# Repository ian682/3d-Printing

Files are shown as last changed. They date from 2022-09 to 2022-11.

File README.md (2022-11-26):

# X5SA Pro EVA 3.0 toolhead mod.

<p align="center">
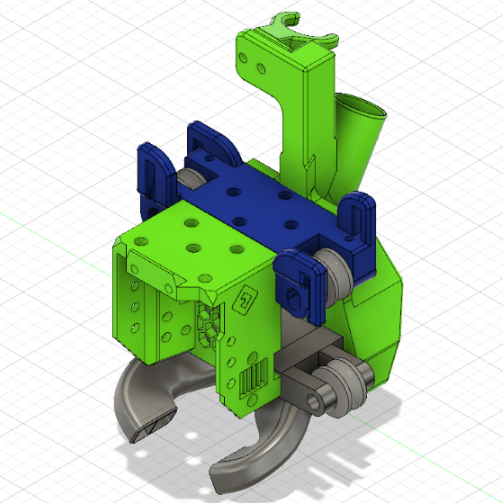
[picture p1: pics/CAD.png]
CAD Layout
  
</p>

Mod is based on the Heat Insert EVA 3.0 project located at https://main.eva-3d.page/

The insert size EVA is modeled for is M3 x D4.6 x L4.0 but this does not have to be exact, i.e. D5.0 or L5.0 inserts should work as well, just might require a bit of clean up of the plastic that's pushed out.

**26-Nov-2022 Update:** Increased OSG Linear bearing adjustment range on "tronxy eva top."  
**24-Nov-2022 Update:** Updated Standard and Volcano duct STLs to stiffen bearing attachment and allow a higher bearing tension range. Also updated step and STL files for the top to adjust geometry for duct changes. Uploaded Step files for standard and volcano ducts, and uploaded fusion 360 ([Project Files](https://github.com/ian682/3d-Printing/blob/main/cad/EVA3/x5sa-pro_eva3_cad.f3d)) for easier CAD maintenance.  
**15-Nov-2022 Update:** Added cable holder for cable bundles.  
**8-Nov-2022 Update:**  Added an additional version of the CPAP back with tilted inlet.   
**30-Oct-2022 Update:** Made CPAP/remote cooling back for 18mm hose.  
**21-Oct-2022 Update:** Increased belt adjustment range on (tronxy eva top.stl) and (tronxy eva top.step) files.

# X5SA Pro EVA 3.0 Mod BOM:

9x Heat inserts  
4x m5 x 30mm screws for OSG Rail Bearings  
14x M5 washers for OSG Rail Bearings  
4x m5 nuts for OSG Rail Bearings  
4x m3 x 40mm screws for mounting universal front to the back 35mm will also work, I only had 40mm on hand. 
2x m3 x 18mm screws for mounting 5015 fans  
4x m3 x 12mm screws osg bearing to rail pre tension  
1x m3 x 10mm screw to mount back to fan duct
2x m3 x 10mm screws to mount cable chain  
2x m3 nuts to mount cable chain  
2x M3 x 30mm screws to mount cable chain bracket to the spacer.  
2x m3 x 6mm screws to mount X-endstop  
1x back ([Dual 5015](https://github.com/ian682/3d-Printing/blob/e409669026c80c21ba648143a89b0567bc5072f4/EVA3/dual%205015%20back.stl) or [Remote Air/CPAP](https://github.com/ian682/3d-Printing/blob/ee2263dbc57e0aab3029547079da61b6ebe15152/EVA3/CPAP%20Back%20Type%202.stl))  
1x X5SA pro EVA Top ([EVA3/tronxy eva top.stl](https://github.com/ian682/3d-Printing/blob/1bf0406b388527418f87d238a55095cb1d77b1a6/EVA3/tronxy%20eva%20top.stl))  
1x X5SA pro EVA fan duct. Choice depends on hotend length. ([Standard Duct](EVA3/EVA_3-0_X5SA-PRO_Standard_Duct.stl) or [Volcano Duct](EVA3/EVA_3-0_X5SA-PRO_Volcano_Duct.stl))  
2x Duct plugs ([EVA3/Duct Hole Plug.stl](https://github.com/ian682/3d-Printing/blob/1bf0406b388527418f87d238a55095cb1d77b1a6/EVA3/Duct%20Hole%20Plug.stl))  
1x Cable chain spacer ([EVA3/cablechain spacer.stl](https://github.com/ian682/3d-Printing/blob/1bf0406b388527418f87d238a55095cb1d77b1a6/EVA3/cablechain%20spacer.stl))  
1x Optional [Cable Holder](https://github.com/ian682/3d-Printing/blob/483a43ff8f26261a6c29b435dc45ae465c516c85/EVA3/Cable%20holder.stl) 

# Main Eva Parts BOM: 
STLs are grabbable from https://main.eva-3d.page/heat_insert/core/corexy/#bill-of-materials  
EVA moddels will list needed screws and heat insert quantaty along with any other needed items. If you do not see a mount for your hotend or extruder, check on printables and thingiverse. Baring that, a lot of models get posted to the EVA section of the Rat Rig Comunity discord https://discord.gg/FekS7xaR New mounts for extruders and hotends are created most days.

Universal front
Hotend mount of your choice  
extruder/drive mount of your choice  
Probe mount of your choice  
shroud if desiered; extra weight and not needed  

# Other Suggested Mods:
Proper belt tension system, suggested version https://www.thingiverse.com/thing:4605033

# Instructions
1st get all needed washers, screws, nuts, ptfe tubing, etc that you need.  
2nd Print desired STL files.  

Print orientation for X5SA pro Parts:  
<p align="center">
  Print orientation
</p>  

Supports will be needed for the X5SA pro EVA top and the bearing arms on the duct. the duct section of the back may or may not need supports depending on how well your printer can bridge.  

After everything is printed, I suggest installing the heat inserts and dry fitting the printed parts together to make sure they all fit and you have everything you need.

Heat insert locations on mod parts:  
<p align="center">
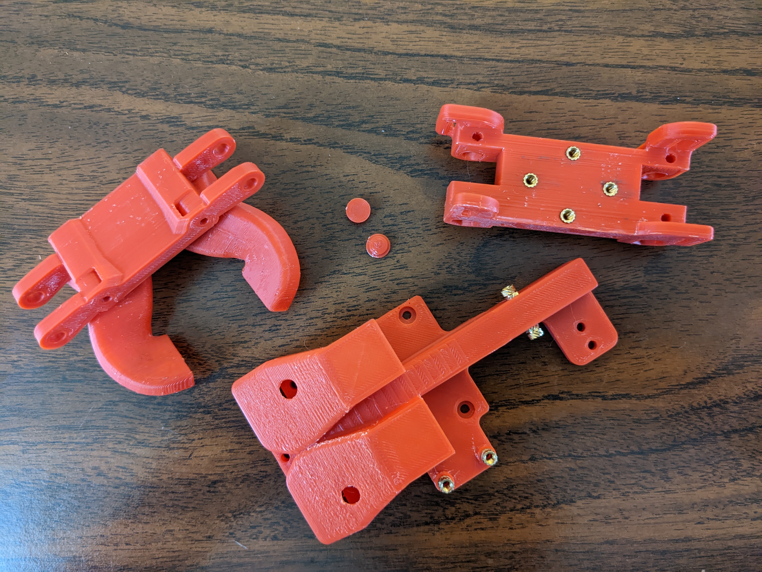
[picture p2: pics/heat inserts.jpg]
Back inserts
  
</p>  

Don't forget the one in the duct:  
<p align="center">
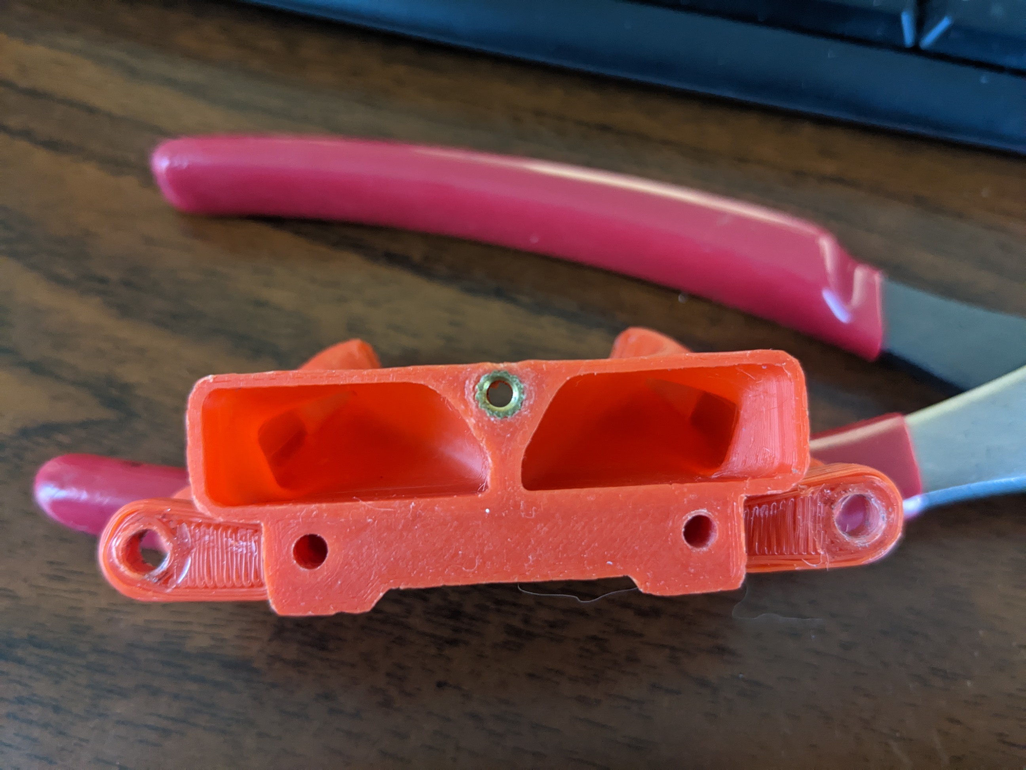
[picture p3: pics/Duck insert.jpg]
Duct insert
  
</p> 
After installing all the heat inserts in the mod parts and the original EVA parts, assuming you have done a drie fit, you are ready to take apart the old tool head and install the new one. You will need the OSG bearing wheels from the old printhead plate, thats the wheels that ride on the rail. I chose to install connectors for the fans, hotend, and ABL sensor. It makes changes and installs much easier.  

Start with installing the OSG bearings in the top and duct bottom. The doct bottom is the easiest of the two to do, so you may want to start with that. Each bearing will get one or two washers, depending on thickness, that go against it on the side that that indents. One side of the bearing protrudes and the other is indented. the washer needs to fit a little loose inside that part of the bearing or it may cause friction. I chose to face the protruding side of the bearings facing the front. It doesn't matter if it faces the front or back, but all 4 must face the same direction.

Top with bearing parts:
<p align="center">
  Top part
</p>   

In this case, all 4 of the bearing required two washers to fill up the space for the bearings. Remember, the washers go on the side that doesn't protrude. For the m5 x 30mm screws, you will need to put a washer on the screw before you start installing it or it will stick out just a little to far. So the order is, washer onto m5 screw > insert screw into top or bottom > insert bearing and start putting the screw through it > two washers > out the other side of the bearing holder arms > nut. The bottom duct will also get another washer just before the nut, but the top does not get that washer. You can tighten the screws on the bottom duct bearings, but leave the ones for the top bearings loose so they can tension on the rail later.

<p align="center">
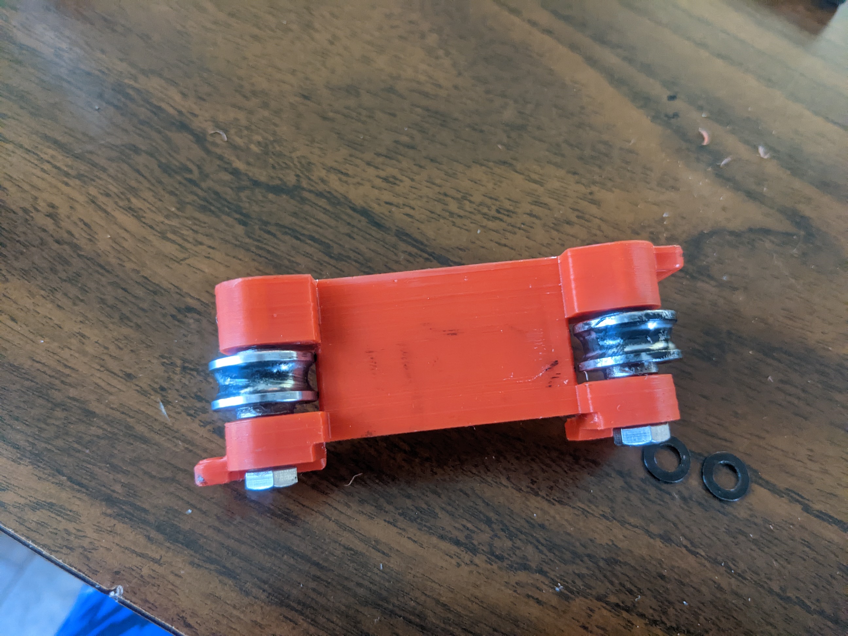
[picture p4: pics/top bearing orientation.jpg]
Top OSG orientation
  
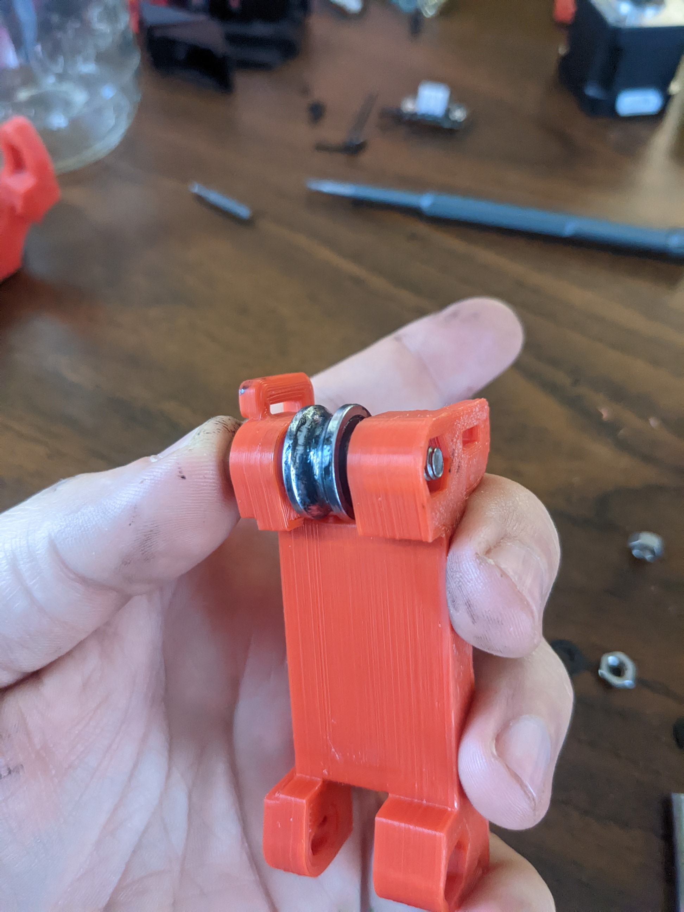
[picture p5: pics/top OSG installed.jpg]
Top OSG
  
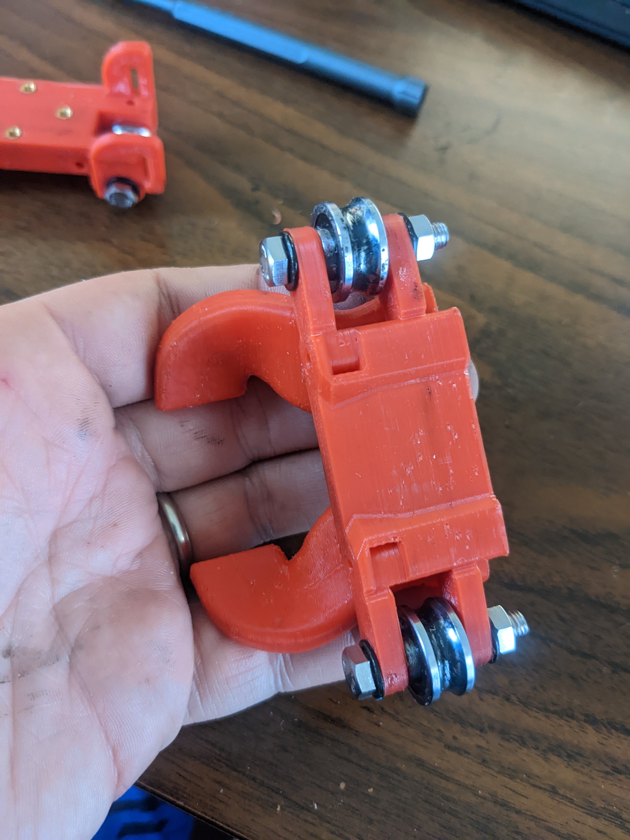
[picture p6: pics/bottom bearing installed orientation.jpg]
Bottom bearing installed
  
</p> 

After this is done, you can build out the Universal front for the print head.

<p align="center">
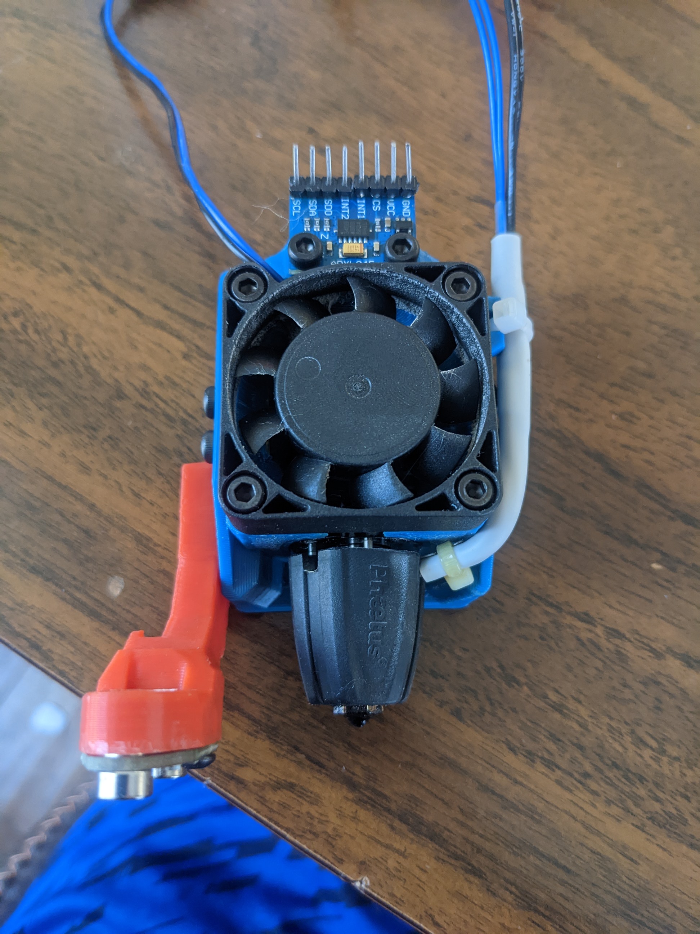
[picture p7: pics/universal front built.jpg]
Universal Front Completed
  
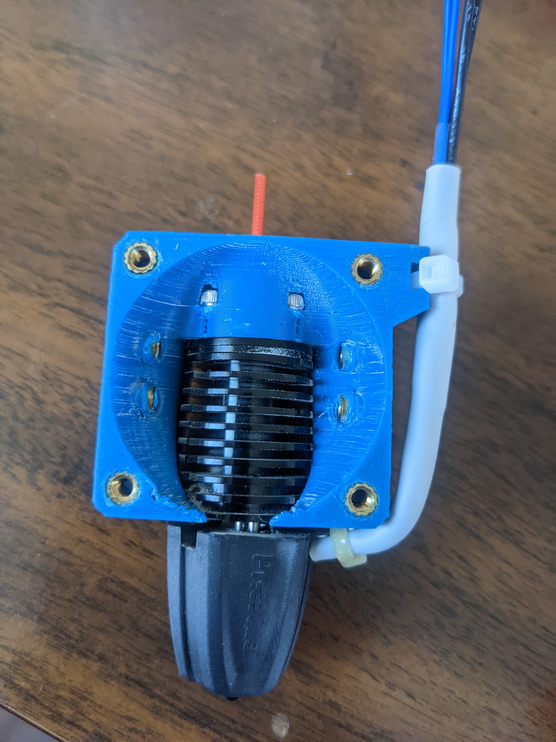
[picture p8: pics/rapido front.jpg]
Hotend Mount front
  
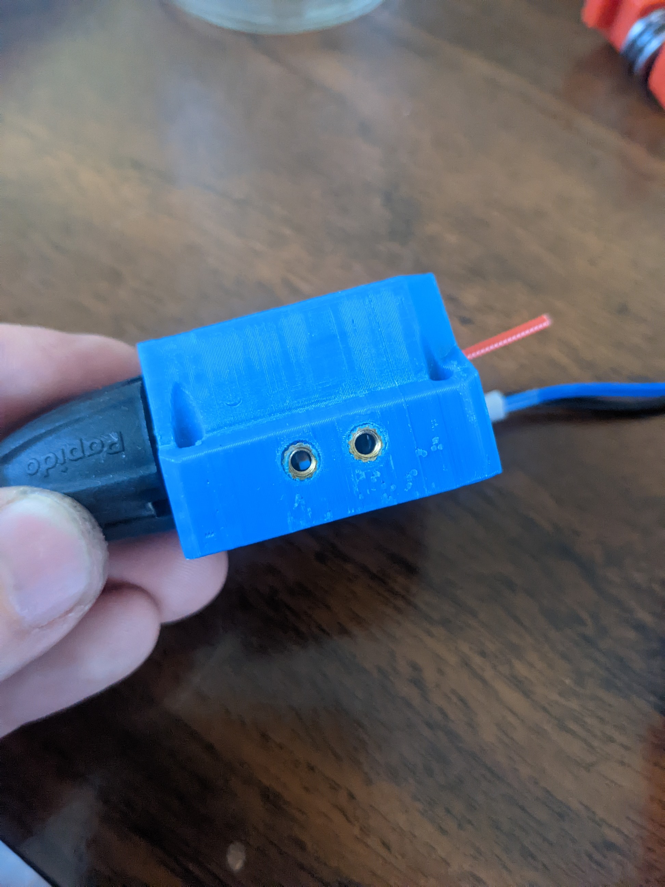
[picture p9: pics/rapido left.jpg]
Hotend Mount left
  
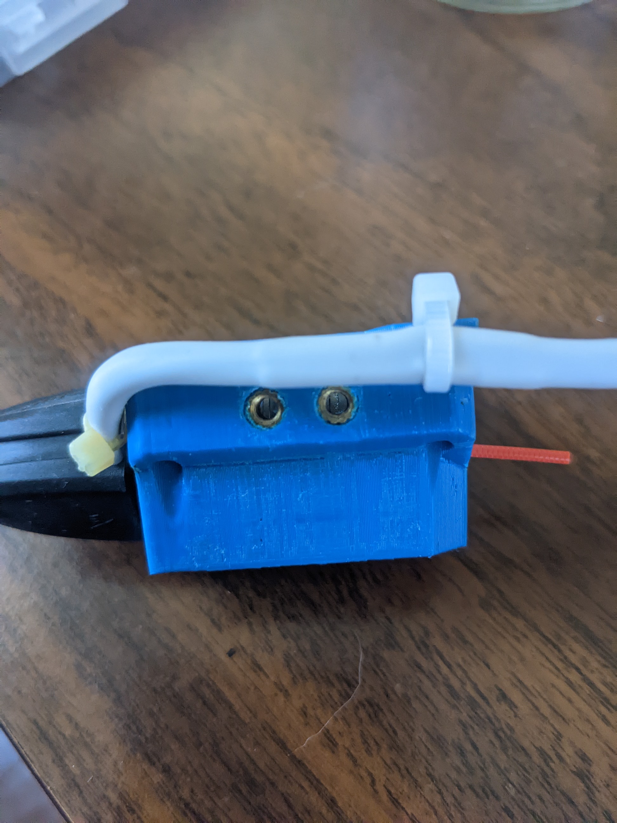
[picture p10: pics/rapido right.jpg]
Hotend mount right
  
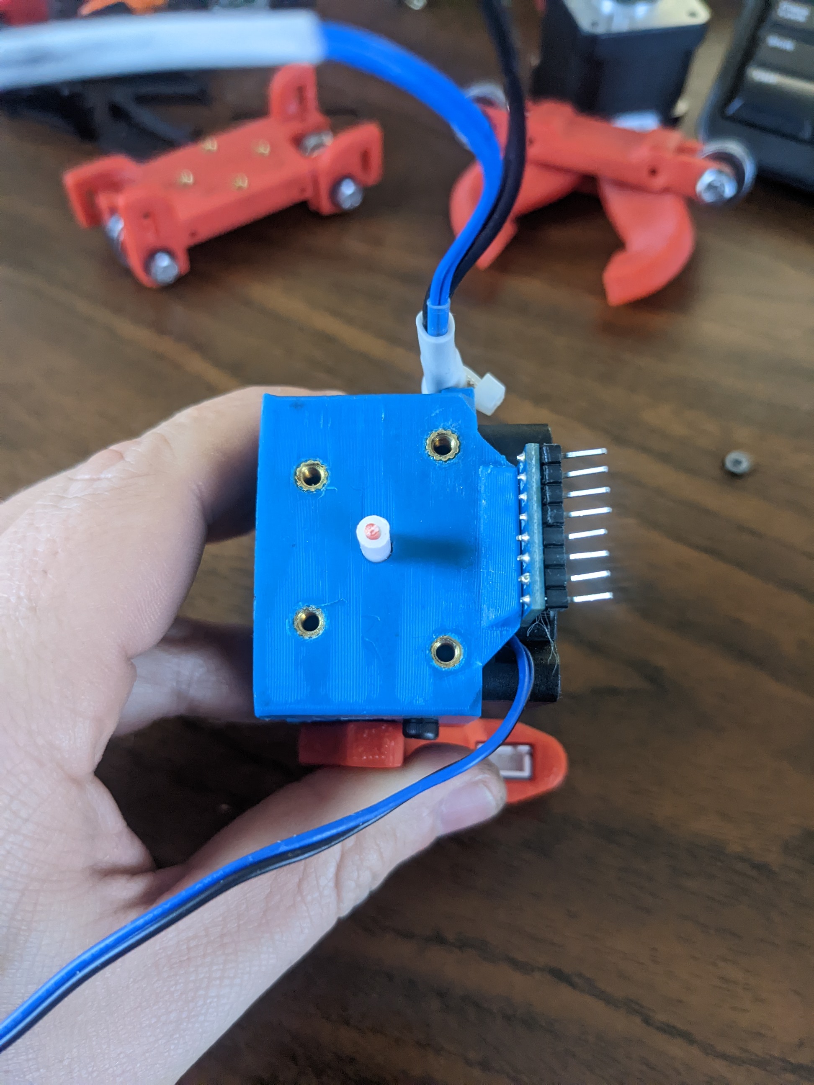
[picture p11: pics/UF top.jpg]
Universal Front top
  
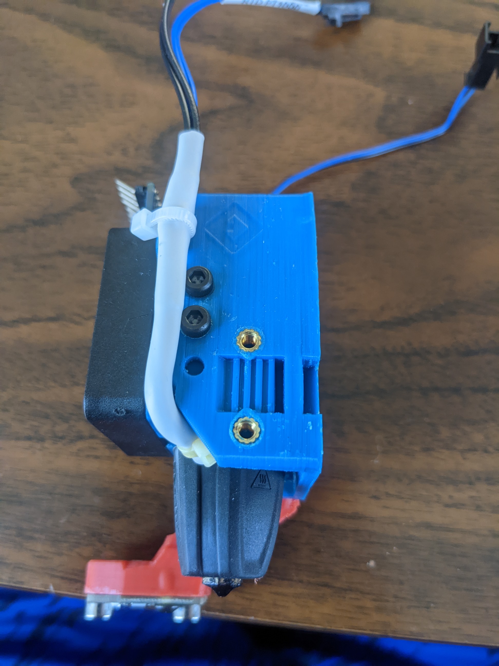
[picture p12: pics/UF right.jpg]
Universal Front right
  
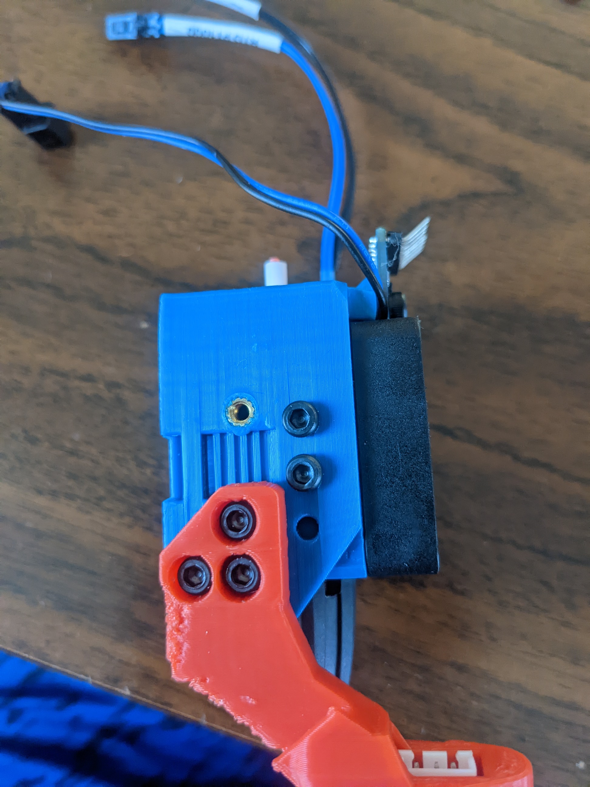
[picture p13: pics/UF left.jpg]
Universal Front left
  
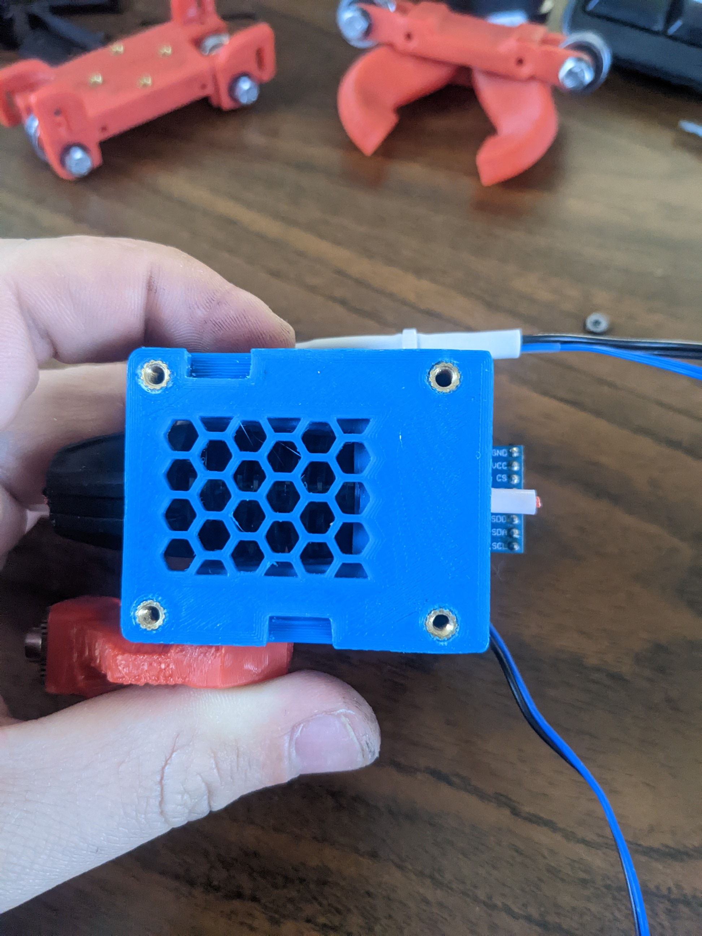
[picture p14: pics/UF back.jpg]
Universal Front back
  
</p>  

At this point you are ready to start installing. There are two changes need so that you don't run into anything at the back of the printer. 1st, install the spacer to push the cable chain holder further back. This gets 2 heat inserts at the back of it and uses two 20mm m3 screws and washers to attach the metal plate to it. You then re-use the m4 screws and t-nuts to insall the spacer on the rail again. 2nd, the stock X5SA cable breakout box need moved so it attaches to the bottom of the back rail instead of the top.
<p align="center">
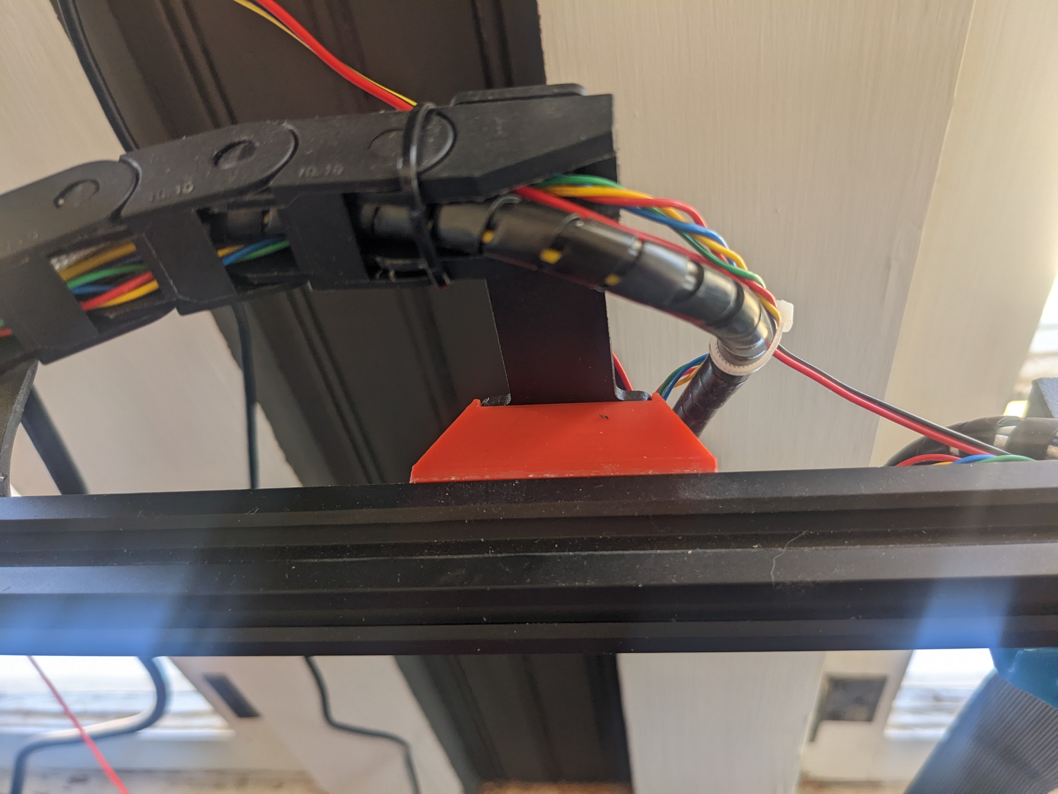
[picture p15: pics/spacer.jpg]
Cable chain spacer
  
  Breakout box moved
</p>  

Next you can mount the cable chain to the back plate of the EVA mod. Two m3 x 10mm screw are used for this along with washers and nuts.
<p align="center">
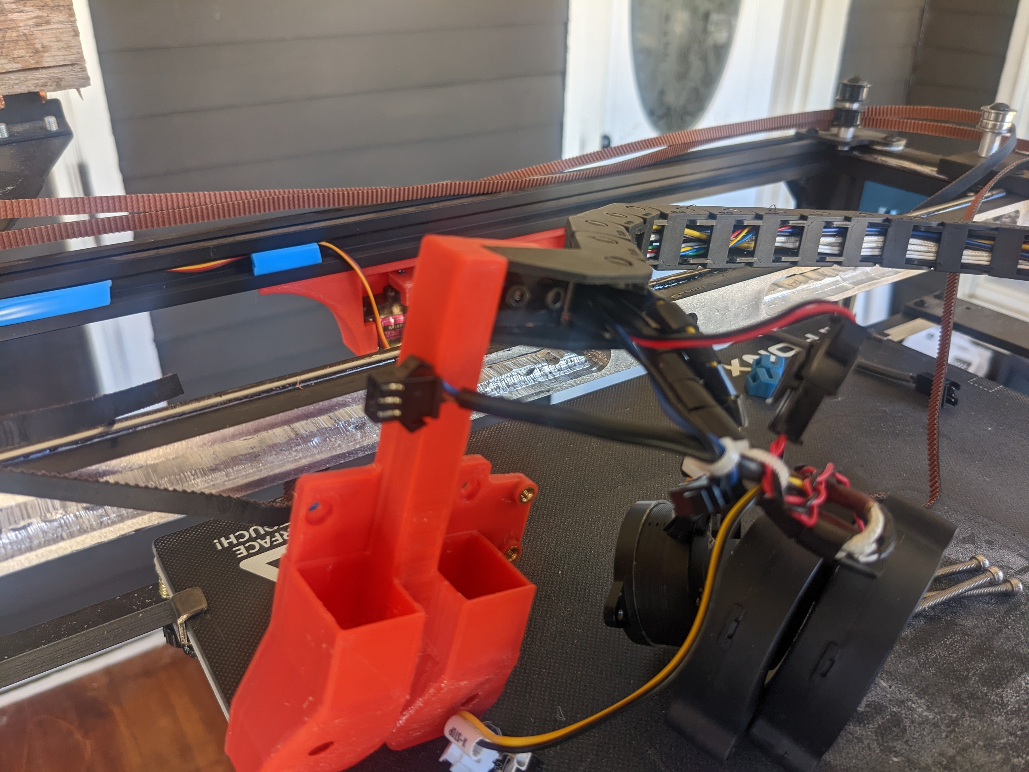
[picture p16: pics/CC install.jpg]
Cable chain installed
  
</p> 

Now install the 4x m3 x 40mm scews through the back plate.
<p align="center">
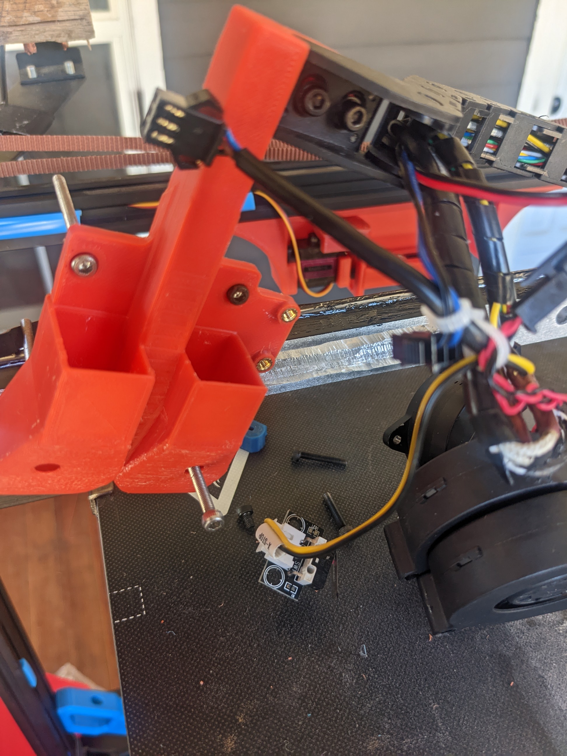
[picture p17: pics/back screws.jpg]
Back screws
  
</p> 

And slide on the bottom duct. Don't miss installing the m3 x 10mm screw from the back into the duct.
<p align="center">
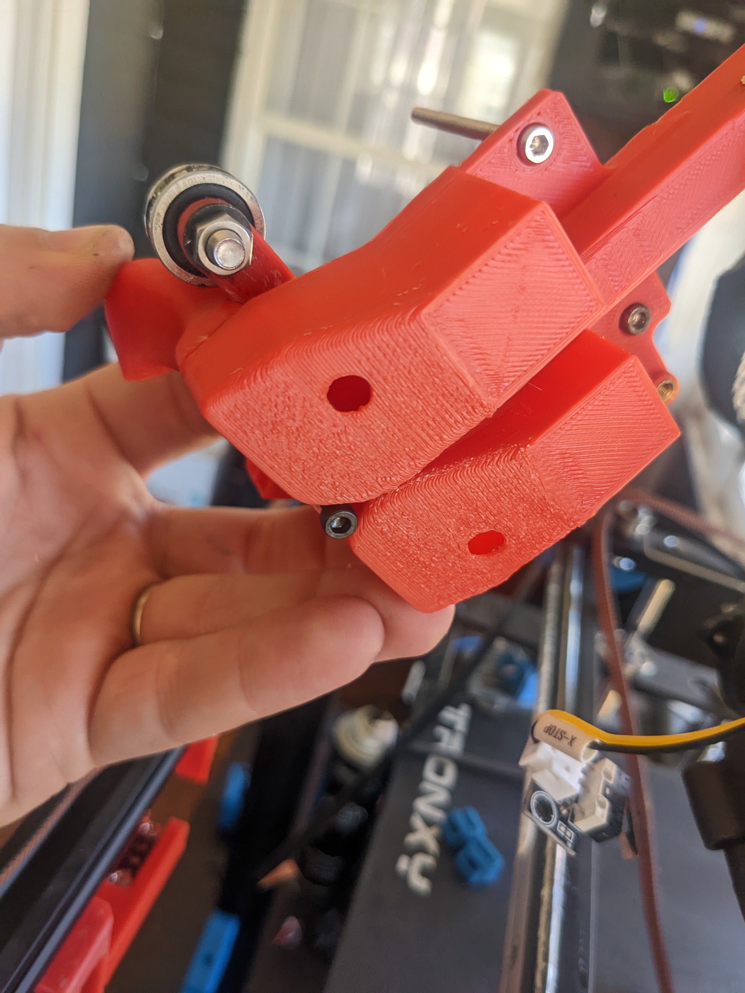
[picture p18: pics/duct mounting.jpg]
Mounting duct
  
</p> 

Move the printhead so that the OSG rail bearings on the duct mate to the bottom of the rail and install the X5SA EVA top onto the m3 x 40mm screws.
<p align="center">
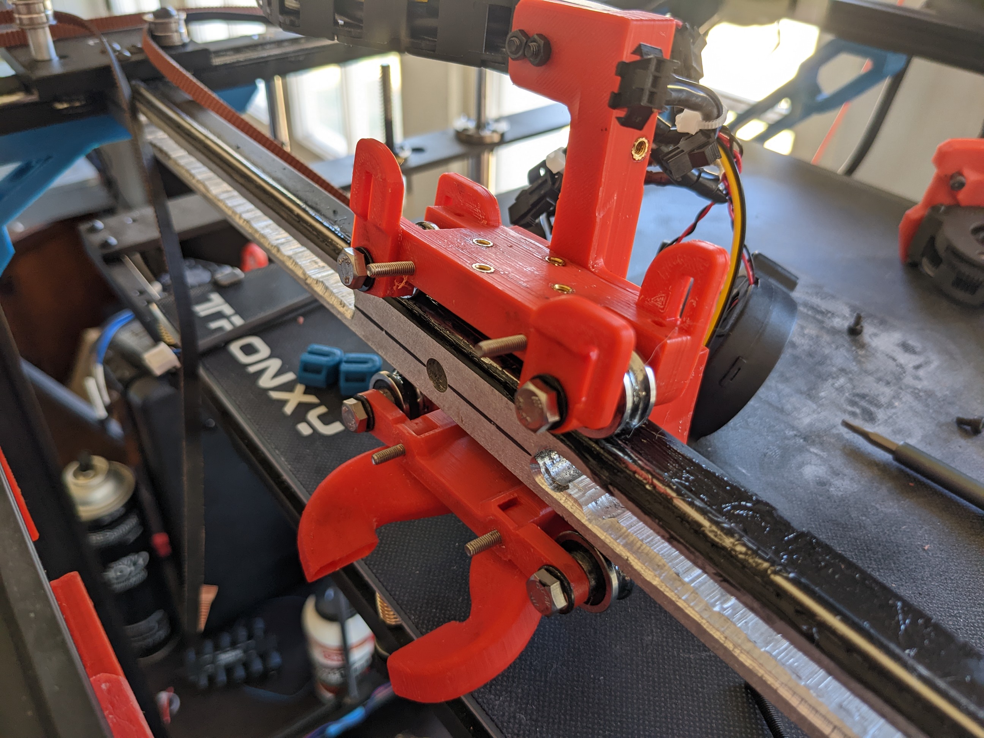
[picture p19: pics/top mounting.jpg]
Mounting top
  
</p> 

Now you can install the universal front onto the printhead. The front mates to the top, bottom, and back with the m3 x 40mm.  
Install the belts, and then the four m3 x 12mm screws to tension the OSG bearing on the rail. Tighten the 12mm screws down untill the bearing screws bottom out in the there slots. At this point you can tighten the bearing screws down. Adjust the belts up or down to align with the pulleys on either side.
<p align="center">
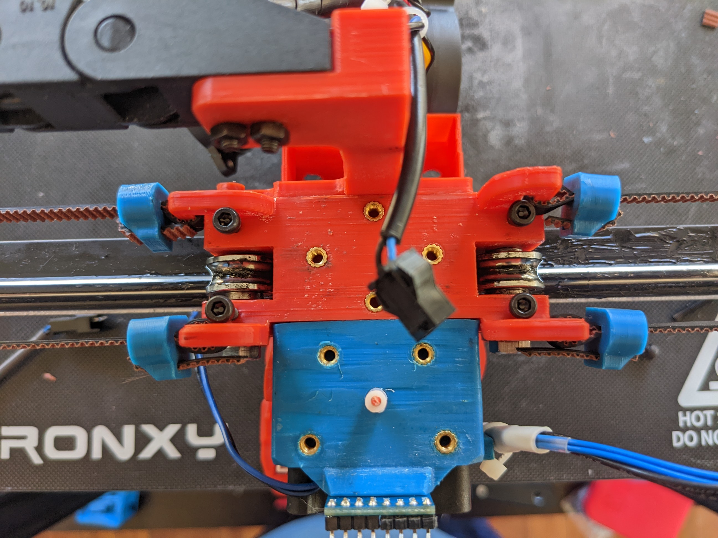
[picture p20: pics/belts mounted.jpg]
Belts and wheel tension
  
</p> 

Install the X-endstop.
<p align="center">
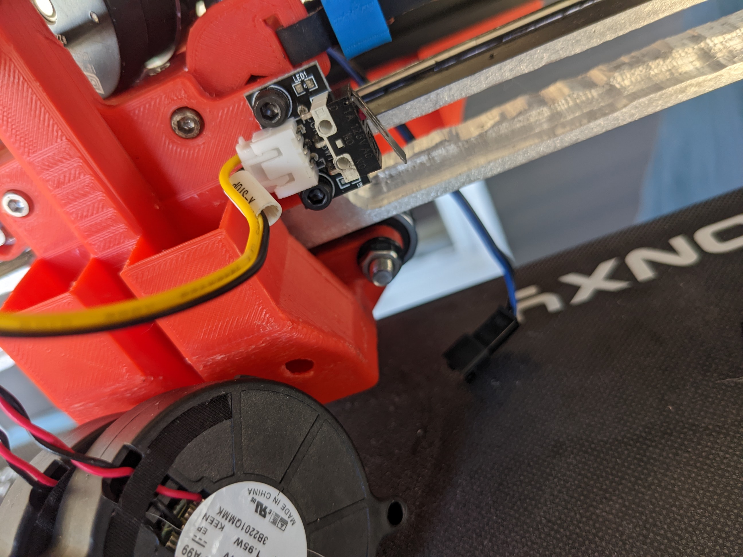
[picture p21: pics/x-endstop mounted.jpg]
X-endstop
  
</p> 

Mount the Part cooling fans.
<p align="center">
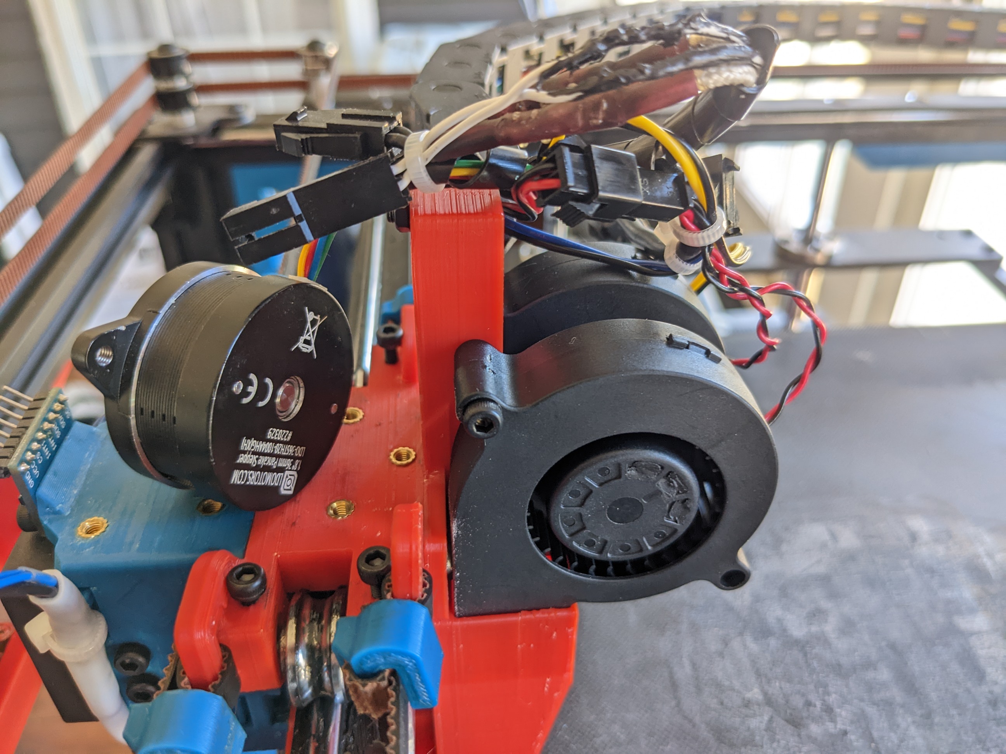
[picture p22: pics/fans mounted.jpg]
Fans mounted
  
</p> 

Install the plugs in the holes in the back ducts
<p align="center">
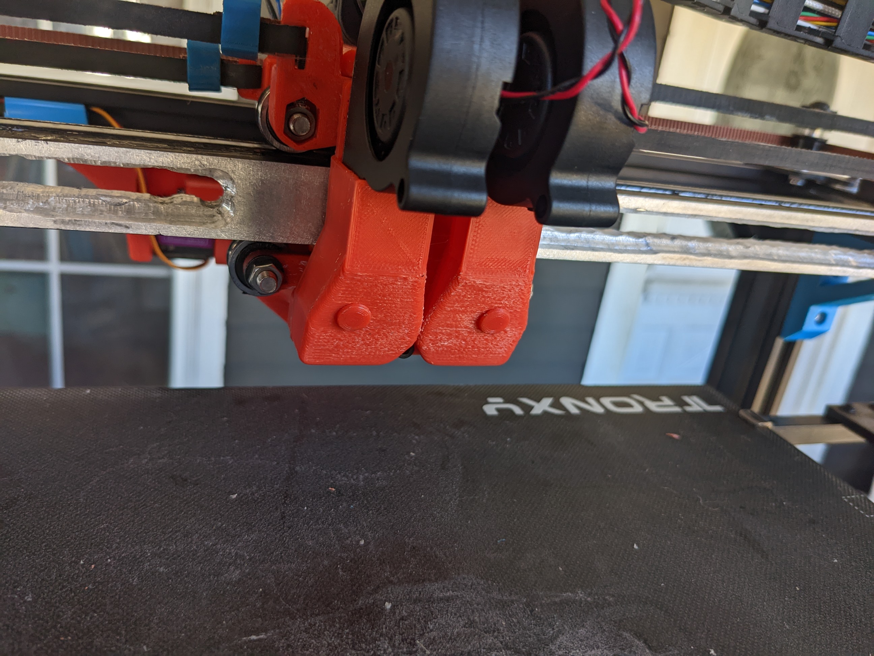
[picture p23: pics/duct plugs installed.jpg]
Duct plugs
  
</p> 

After that, install the extruder of your choice, cleanup the wiring, and tune the printer. I would also encurage installing a means to accuratly tune the belt tension, such as the one at the top of this page. I suggest using Andrew Ellis' [tuning guide](https://github.com/AndrewEllis93/Print-Tuning-Guide).

Congratulations, you are now running the EVA 3 printhead on your TronXY X5SA Pro
<p align="center">
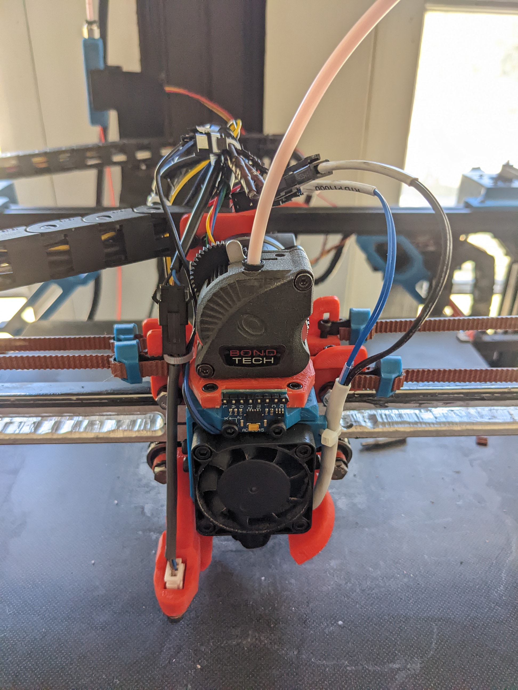
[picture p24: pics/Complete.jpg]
Finished
  
</p>

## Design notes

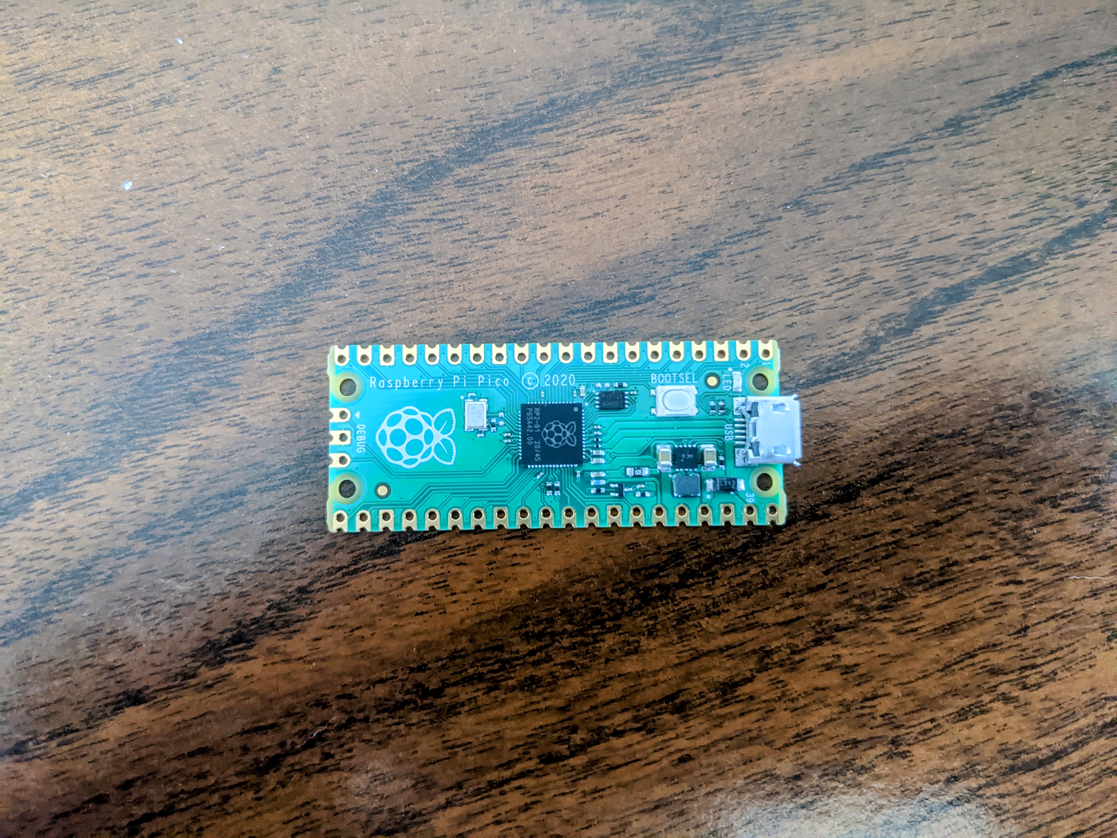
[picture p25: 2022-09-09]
servo_dock/pictures/PXL_20220909_153649649~2.jpg

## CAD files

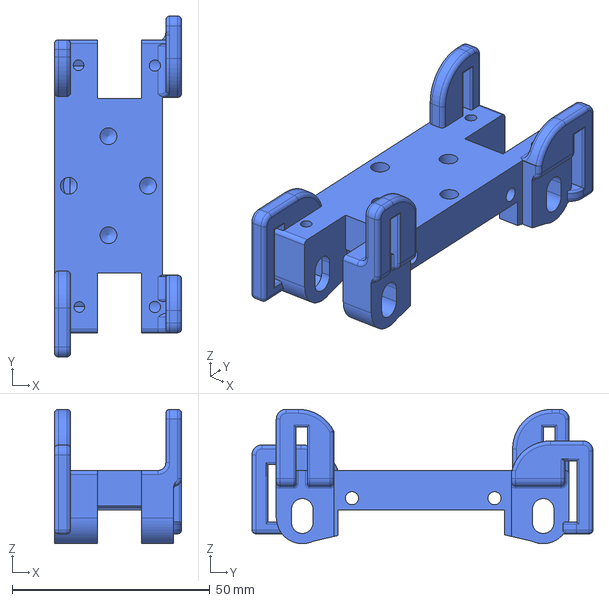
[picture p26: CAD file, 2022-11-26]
cad/EVA3/tronxy eva top.step
32.1 x 86.1 x 34.0 mm

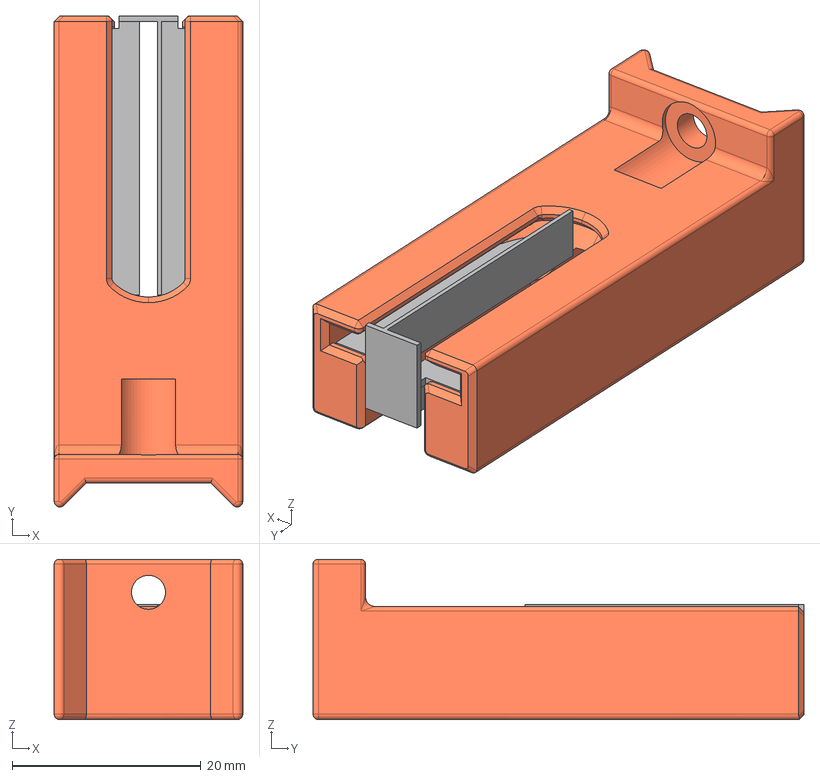
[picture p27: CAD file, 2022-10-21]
cad/servo_dock/adjustable_dock_lower.step
20.0 x 52.1 x 17.0 mm

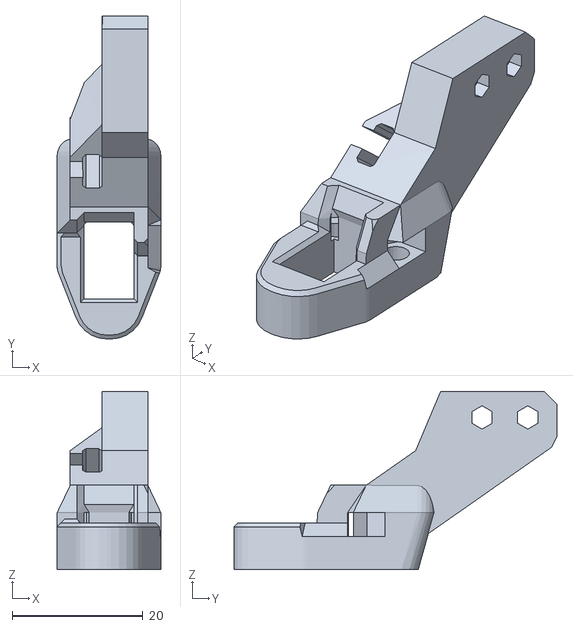
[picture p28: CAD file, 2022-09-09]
euclid_probe/EuclidMount_EVA3_0_v05.stl
15.9 x 49.5 x 27.3

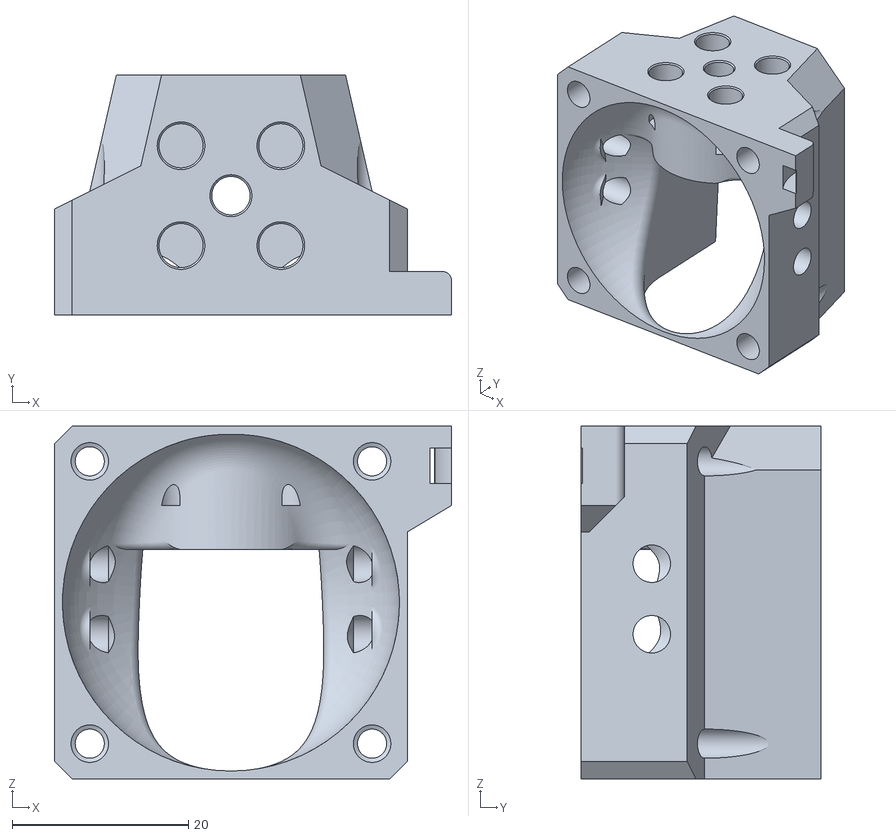
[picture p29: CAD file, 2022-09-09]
EVA3/hotend_rapido_fi.stl
45.0 x 27.2 x 40.0

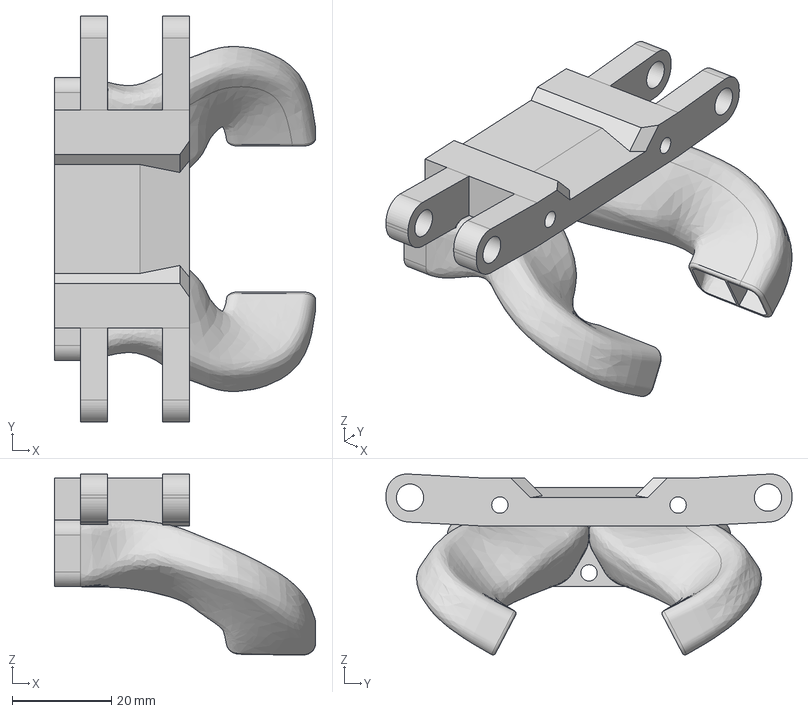
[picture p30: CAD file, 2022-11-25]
cad/EVA3/EVA_3-0_X5SA-PRO_Volcano_Duct.step
52.7 x 82.0 x 36.5 mm

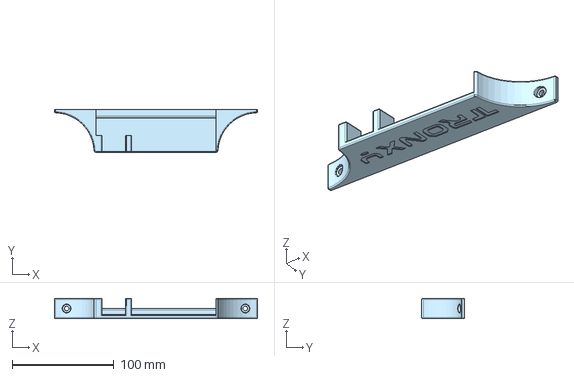
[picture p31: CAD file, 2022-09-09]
cad/servo_dock/servo dock front mount.step
200.0 x 42.0 x 20.0 mm

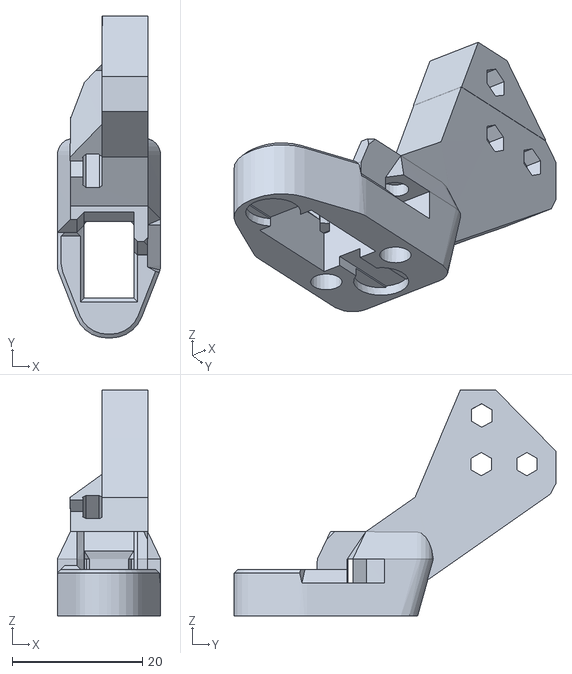
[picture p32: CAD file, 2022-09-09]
euclid_probe/EVA3_Euclid_Probe_Mount.stl
15.9 x 49.4 x 34.7

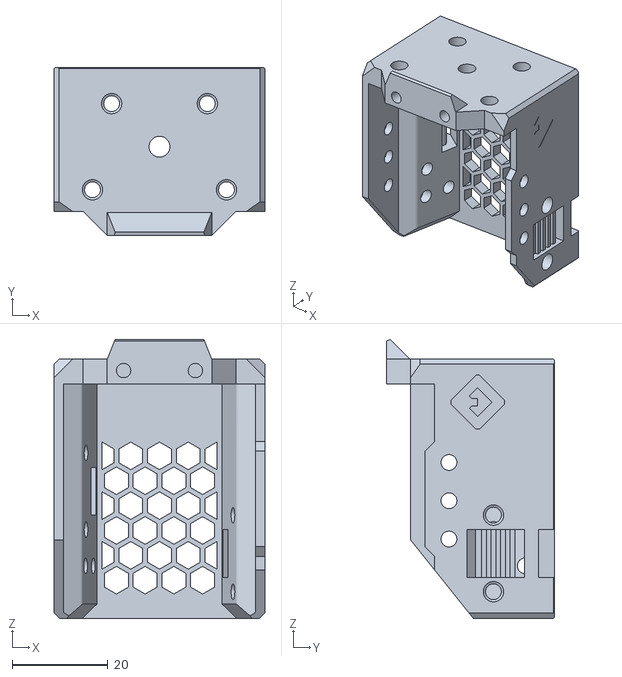
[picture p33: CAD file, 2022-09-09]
EVA3/front_universal_fi.stl
44.0 x 35.0 x 58.3

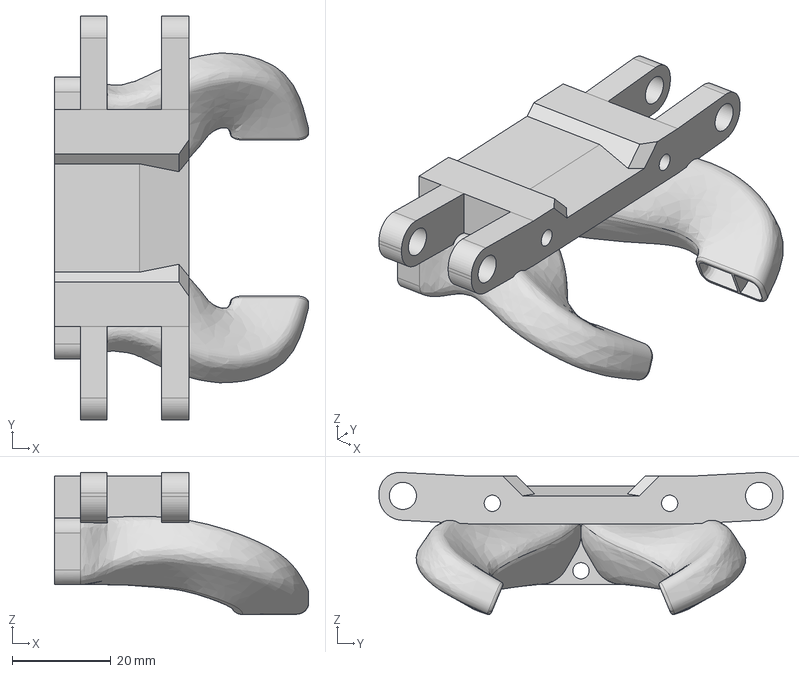
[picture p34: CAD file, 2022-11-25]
cad/EVA3/EVA_3-0_X5SA-PRO_Standard_Duct.step
51.6 x 82.0 x 28.9 mm

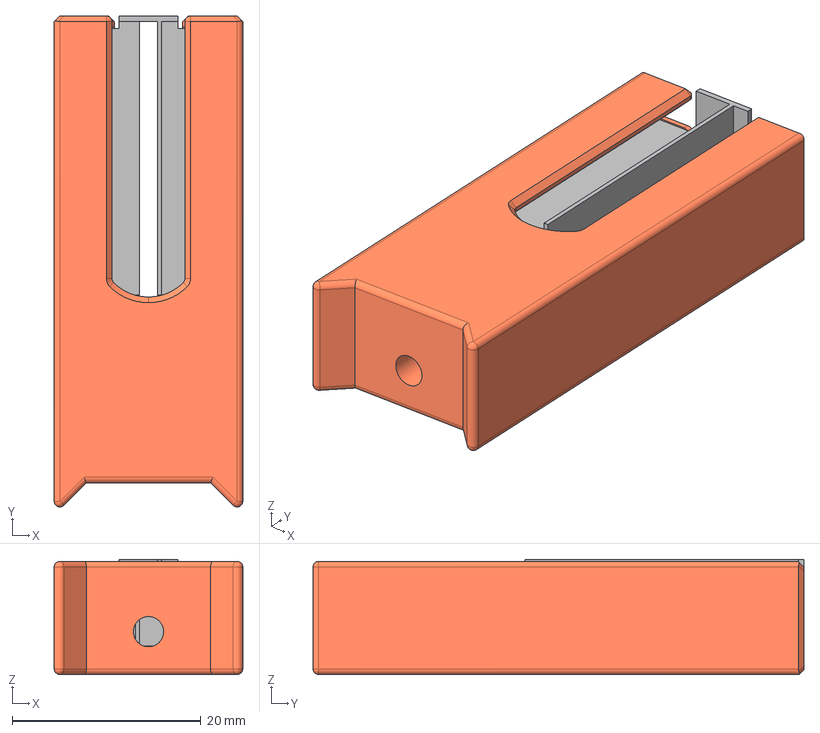
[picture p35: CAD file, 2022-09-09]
cad/servo_dock/adjustable_dock.step
20.0 x 52.1 x 12.2 mm

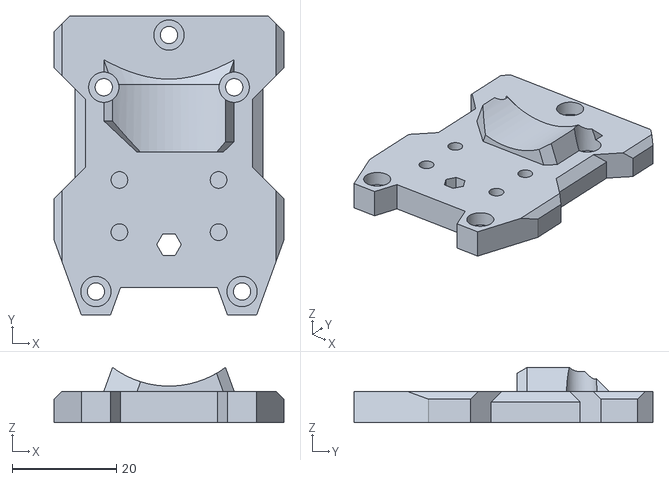
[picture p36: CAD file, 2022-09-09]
EVA3/drive_lgx_lite.stl
44.0 x 57.3 x 10.6

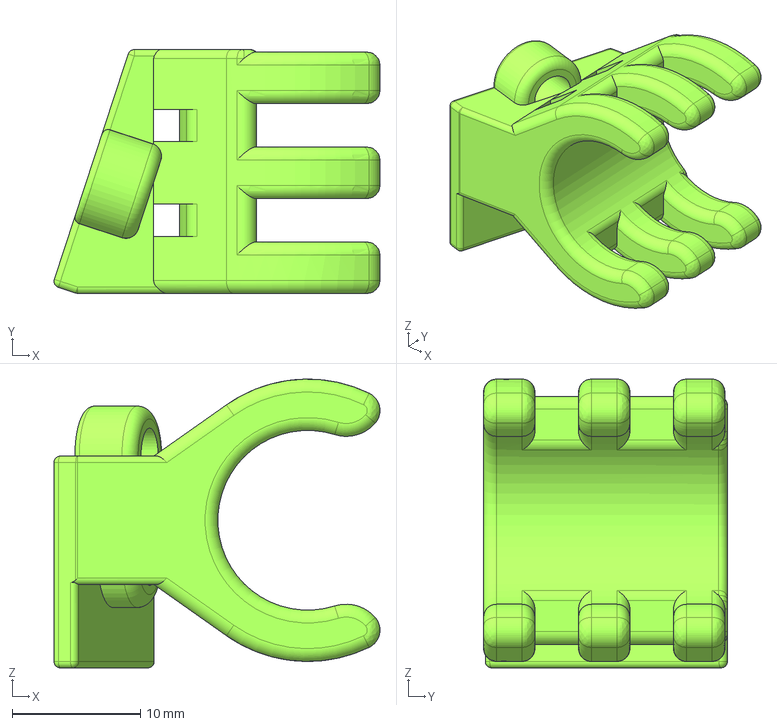
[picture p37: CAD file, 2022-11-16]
cad/EVA3/Cable holder.step
25.4 x 19.0 x 22.5 mm

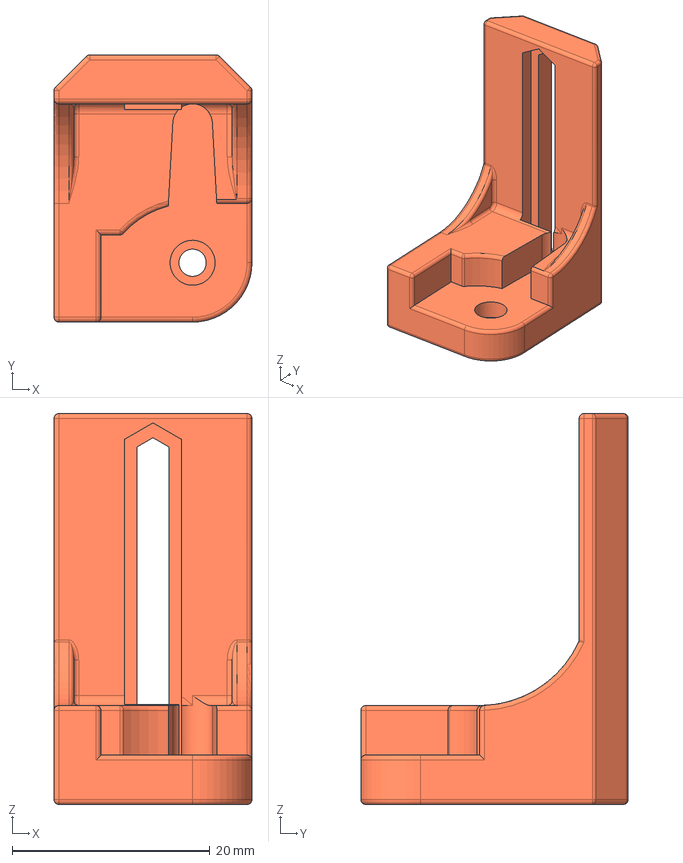
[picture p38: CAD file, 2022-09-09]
cad/servo_dock/Arm.step
20.0 x 27.0 x 39.5 mm

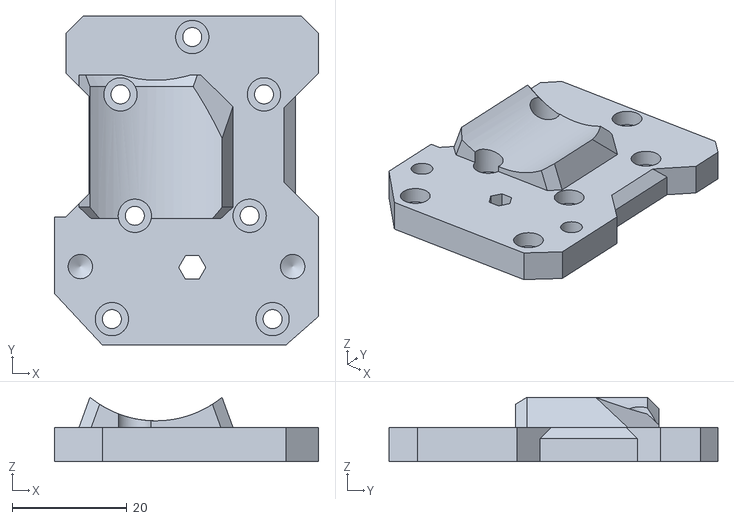
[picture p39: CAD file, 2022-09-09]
EVA3/drive_orbiter_2.0_fi.stl
46.0 x 57.3 x 11.2

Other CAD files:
cad/EVA3/CPAP Back Type 2.step
cad/EVA3/tronxy eva 3 CPAP-Remote air back.step
cad/EVA3/cablechain spacer.step
cad/EVA3/dual 5015 back.step
EVA3/CPAP Back Type 2.stl
EVA3/Cable holder.stl
EVA3/Duct Hole Plug.stl
EVA3/cablechain spacer.stl
EVA3/dual 5015 back.stl
EVA3/tronxy eva 3 CPAP-Remote air back.stl
EVA3/tronxy eva top.stl
cad/EVA3/Duct Hole Plug.step
cad/EVA3/x5sa-pro_eva3_cad.f3d
servo_dock/Arm.stl
servo_dock/adjustable_dock.stl
servo_dock/adjustable_dock_lower.stl
servo_dock/servo dock front mount.stl

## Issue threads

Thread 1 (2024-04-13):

toolhead - no way to get it straight

seBASTELian2, 2024-04-13:
It is not possible for me to mount the tool head straight on the gantry. No matter how I adjust it, it always tilts slightly backwards. I prepared everything as described and now I'm in a mess because nothing works without a straight basis. What am I doing wrong?? 4 days and nothing changes

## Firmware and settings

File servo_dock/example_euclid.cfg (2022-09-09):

## The following is EXAMPLE configuration; it is intended to guide you in the
## configuration of the Euclid probe for YOUR printer.
##
## When incorporating this config into your own, make sure you address all
## comment markers starting with "@TODO".  Failure to do so could result in
## damage to your probe, your printer, or your pride.
##
##
## This example is for a fixed dock, fixed gantry/carriage and moving bed motion
## system like RailCore, Ender5, V-Core3, etc. Delta printes will be similar.
##
## Moving gantry printers like Voron need a few tweaks to ensure proper
## clearances and leveling procedures; some hints are provided inline below.
##
## Array variables implementation and macro setups credited to Brian Lalor,
## yolo-dubstep#8033 on Discord. See https://github.com/blalor/vcore3-ratos-config
## for updates and details.
##

## @TODO the following is a hardware probe config for the hardware configuration.
## it can appear in either the printer.cfg OR in the euclid.cfg, not both.
## see https://euclidprobe.github.io/05_klipper.html for more details.
##
##
# [probe]
# pin: ^PG15
# x_offset: -27.942
# y_offset: -16.75
# z_offset: 8.514
# speed: 5
# samples: 2
# samples_result: average
# sample_retract_dist: 5.0
# samples_tolerance: 0.05
# samples_tolerance_retries: 3
# lift_speed: 30

# Below is an example bed diagram to correlate with macros and movements below.
#  __________________________________________________________________________
#  |                                                                        |
#  |                                                                        |
#  |                                                                        |
#  |                                                                        |
#  |                                                                        |
#  |                                                                        |
#  |                                                                        |
#  |                                                                        |
#  |                                                                        |
#  |                                                                        |
#  |                                                                        |
#  |                                                                        |
#  |                                                                        |
#  |                                                                        |
#  |                                                                        |
#  |                                                                        |
#  |                                                                        |
#  |                                                                        |
#  | * Dock Exit Position                                                   |
#  |   X18,Y290                                                             |
#  |                                                                        |
#  |                                                                        |
#  |                                                                        |
#  |                                                                        |
#  |                                                                        |
#  |   X18,Y330  X48,Y330       X100,Y330                                   |
#  | * Dock   * Dock Side  * Dock Preflight                                 |
#  |________________________________________________________________________|
#

[gcode_macro EuclidProbe]
description: config vars for Euclid probe deploy/stow

## @TODO Replace the coordinates to suit your printer
variable_position_preflight: [ 100, 330 ] # position for probe to have clear path to dock
variable_position_side:      [  48, 330 ] # position for probe near dock to swipe on/off
variable_position_dock:      [  18, 330 ] # dock position
## @TODO if your printer has a fixed Z-Endstop that you will use define it here
## @TODO for example Voron Trident
## variable_position_zstop:      [ 150,250 ] # zstop position

## exit/re-entry staging
variable_position_exit:      [   18, 290 ] # exit position

## clearance between the toolhead and bed when traveling to pick up the probe
variable_bed_clearance: 20

## probe dock height
## @TODO If the toolhead can move vertically in relation to the probe dock
## @TODO height(such as attached to the be on a moving-gantry printer like a
## @TODO Voron 2.4), set this to the Z position of the probe dock.
# variable_dock_height: 15

## move speeds in mm/min
variable_move_speeds: 18000

## internal state variables; not for configuration!
variable_batch_mode_enabled: False
variable_probe_state: None

gcode:
    RESPOND TYPE=command MSG="{ printer['gcode_macro EuclidProbe'] }"

## Servo Dock Section
#
[servo euclid]
pin: adxl:gpio4 #Probe Connection on your board
initial_angle: 90
maximum_servo_angle = 180
minimum_pulse_width = 0.0005
maximum_pulse_width = 0.0024

[gcode_macro SERVO_OUT]
gcode:
    SET_SERVO SERVO=euclid ANGLE=0

[gcode_macro SERVO_IN]
gcode:
    SET_SERVO SERVO=euclid ANGLE=90
	SET_SERVO SERVO=euclid WIDTH=0


# @TODO The homing override is machine specific.  This example is for a
# @TODO fixed-gantry/moving-bed printer such as the Rat Rig V-Core 3.  Ensure you
# @TODO only have [homing_override] defined in one place in your Klipper config
# @TODO (typically here or in printer.cfg).  It's particularly important to make
# @TODO sure the probe is picked up before attempting to home the Z axis.
[homing_override]
axes: z
set_position_z: -5
gcode:
    {% set euclid_probe = printer["gcode_macro EuclidProbe"] %}

    # @TODO Remove this comment and the following once you've verified that the
    # @TODO probe can be deployed without the bed, dock, or toolhead colliding.
#    M112

    G90

    # force the bed and toolhead apart
    SET_KINEMATIC_POSITION Z=0
    G0 Z{ euclid_probe.bed_clearance } F500

    # home Y and X, Y first to avoid running into the dock
    {% if "y" not in (printer.toolhead.homed_axes | lower) %}
        G28 Y
    {% endif %}

    {% if "x" not in (printer.toolhead.homed_axes | lower) %}
        G28 X
    {% endif %}

    ## @TODO If you are using Euclid to function as a Z-Endstop, then you need to deploy it.
    ## @TODO If you are using a fixed Z-stop, then comment out the next line
    DEPLOY_PROBE

    # @ TODO  home Z at bed center with Euclid Probe
    G0 Y{ printer.toolhead.axis_maximum.y/2 } X{ printer.toolhead.axis_maximum.x/2 } F{ euclid_probe.move_speeds }
    G28 Z

    # after 'G28 Z' the probe stays in contact with the bed; move it away bed_clearance height.
    G0 Z{euclid_probe.bed_clearance} F500

    ## @TODO If you are using Euclid to function as a Z-Endstop, then you need to stow  it.
    ## @TODO If you are using a fixed Z-stop, then comment out the next line
    STOW_PROBE

[gcode_macro _ASSERT_PROBE_STATE]
description: ensures probe is in a known state; QUERY_PROBE must have been called before this macro!
gcode:
    ## QUERY_PROBE manually-verified results, when microswitch not depressed
    ## "TRIGGERED" -> 1 :: probe stowed
    ## "open"      -> 0 :: probe deployed
    {% set last_query_state = "stowed" if printer.probe.last_query == 1 else "deployed" %}

    {% if params.MUST_BE != last_query_state %}
        { action_raise_error("expected probe state to be {} but is {} ({})".format(params.MUST_BE, last_query_state, printer.probe.last_query)) }
    {% else %}
        ## all good; update state
        SET_GCODE_VARIABLE MACRO=EuclidProbe VARIABLE=probe_state VALUE="'{ last_query_state }'"
    {% endif %}


[gcode_macro ASSERT_PROBE_DEPLOYED]
description: error if probe not deployed
gcode:
    # wait for moves to finish, then pause 0.25s for detection
    M400
    G4 P250

    QUERY_PROBE
    _ASSERT_PROBE_STATE MUST_BE=deployed


[gcode_macro ASSERT_PROBE_STOWED]
description: error if probe not stowed
gcode:
    # wait for moves to finish, then pause 0.25s for detection
    M400
    G4 P250

    QUERY_PROBE
    _ASSERT_PROBE_STATE MUST_BE=stowed


[gcode_macro EUCLID_PROBE_BEGIN_BATCH]
description: begin euclid probe batch mode
gcode:
    SET_GCODE_VARIABLE MACRO=EuclidProbe VARIABLE=batch_mode_enabled VALUE=True
    RESPOND TYPE=command MSG="Probe batch mode enabled"


[gcode_macro EUCLID_PROBE_END_BATCH]
description: end euclid probe batch mode and stow probe
gcode:
    SET_GCODE_VARIABLE MACRO=EuclidProbe VARIABLE=batch_mode_enabled VALUE=False
    RESPOND TYPE=command MSG="Probe batch mode disabled"
    STOW_PROBE
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

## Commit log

2022-09-09 Add existing file
    [Arm.step, Arm.stl, EVA3_Euclid_Probe_Mount.stl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]
2022-10-21 Delete tronxy eva top.stl
    Uploading an updated version to increase belt adjustment range.
    [tronxy eva top.stl]
2022-10-21 Add files via upload
    Updated model to increase belt adjustment range.
    [tronxy eva top.stl]
2022-10-21 Delete tronxy eva top.step
    uploading new cad.
    [tronxy eva top.step]
2022-10-21 Add files via upload
    Updated CAD for increased belt adjustment range.
    [tronxy eva top.step]
2022-10-22 Delete cablechain spacer.stl
    updating file.
    [cablechain spacer.stl]
2022-10-22 Add files via upload
    updated file
    [cablechain spacer.stl]
2022-10-22 Delete cablechain spacer.step
    updating file
    [cablechain spacer.step]
2022-10-22 Add files via upload
    updated file.
    [cablechain spacer.step]
